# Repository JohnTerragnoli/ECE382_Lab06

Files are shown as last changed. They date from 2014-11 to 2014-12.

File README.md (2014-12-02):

ECE382_Lab06
============

#Purpose

The purpose of this lab is to use pulse width modulation to use an MSP430 to control a small robot car.  This will be done with the help of other devices, such as driver and regulator chips, IR sensors, and a remote.  

#Prelab
**Things to accomplish**

1. Use A regulator to power the MSP430.
2. How to use hardware to achieve robot control (driver).
3. Consider additional hardware you'll need (regulator, motor driver chip, decoupling capacitor).
4. Which pins will output which signals you need.
5. Which side of the motor will you attach these signals to.
6. How will you connect these extra parts?
7. How to use these signals to achieve forward/back/left/right movement.
8. consider how you will setup the PWM subsystem to achieve control.
9. what are the registers you'll need to use.
10. which bits in the registers are important?
11. what's the initialization sequence you'll need?
12. Try to build simple commands, such as moving one motor one direction.
13. Combine simple commands to make complex ones, like just moving in a specific direction.
14. Determine worst-case current draw from your motors (**motor stall current**)

**Remember**

1. Never send voltage to both terminals at once.  

##Hardware Planning Process

**How to Power the MSP430**
1. The MSP430 can only accept 3.3v, whereas the source we have can only output 5v.  We need to use a regulator to drop this voltage.  Should maybe use a small capacitor across the 5V rail to smoth high frequency noise.  This capacitor should be ~0.1uF.  
2. To determine how this should be hooked up, this datasheet was consulted.  It deals with [voltage regulators](http://www.ece382.com/datasheets/LD1117V33.pdf).  This schematic is used below:

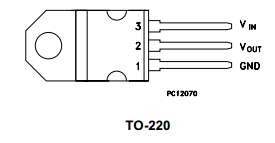
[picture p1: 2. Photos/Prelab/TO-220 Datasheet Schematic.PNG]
TO-220 Config


This was then attached to the MSP430 in the following way:

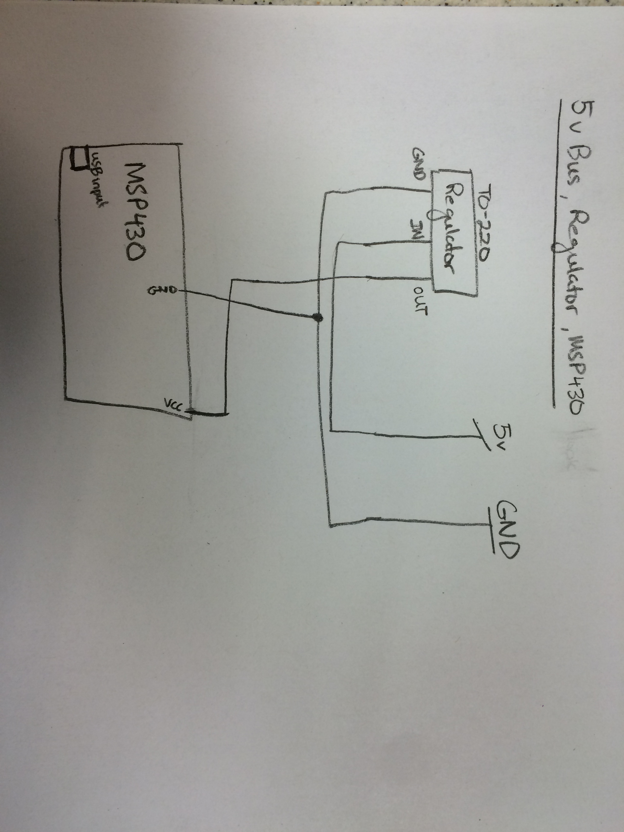
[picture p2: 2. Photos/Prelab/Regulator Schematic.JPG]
MSP Regulator


**Adding the Driver**
The purpose of the driver allows the MSP430 to control the motors without burning up due to the current requirements.  The datasheet for the Quadruple Half Driver can be seen [here](http://www.ece382.com/datasheets/SN754410.pdf).  

Its pinout and function table may be seen below: 

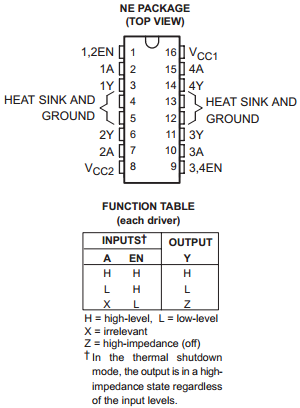
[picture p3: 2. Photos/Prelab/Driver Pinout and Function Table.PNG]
Driver Config


Next, to understand how to hook this up to the motors and to the MSP430, we must first decide how the program will run.  For simplicity sake, I plan on using two individual output signals for the forward direction, and a common output signal for the reverse.  This should make the design easier since we are not required to turn backwards. Therefore, hooking up the driver to the MSP430 and the motos should be relatively easy.  

First, we note that V_cc1 must be between 4.5 and 5.5 volts, as seen in the datasheet.  Therefore, V_ccs1 must be hooked up to the 5v source, which is the only source within range available on the robot.  

Secondly, V_cc2 is meant for the outputs, as noted on the datasheet.  It must be between the range of 4.5 and 36v.  Knowing that the voltage to provide the motors must be greater than 5v, we know that V_cc2 must be hooked up to the 12v source, the only other available source on the chip.  Also, I remember when reading the prelab instructions that if 12v are used, then the duty cycle may not exceed 60%.  This will hurt the motor.  Just something to keep in mind for later.  

Thirdly, the 1,2 EN and 3,4 EN pins will be involved in the logic of the circuit.  Their main purpose is to enable the outputs when their voltage is high.  It would make the most sense for the purposes of this design to make them always high.  Then, the outputs 1-4, or the outputs which are sent to the motors, will be determined entirely by the code.  I think this will lead to fewer complications later on.  Therefore, to do this, the 5v bus will be connected to pins 1, 9, and 16.  

Fourth, the ground must be established for the driver chip.  Based on the pinout, GND is pins 4, 5, 12, and 13.  Therefore, all of these are connected to GND.  

Fifth, I will decide where the inputs (the outputs from the MSP430 go on the driver) will go on the driver chip.  I decide to put one set into pins 3A and 4A, which are pins 10 and 15, respectively.  These inputs will control the right motor through pins 11 and 14, which are ground and input for the right motor, respectively.  Then, the next set of intputs will go into 1A and 2A, which are pins 2 and 7, respectively.  It's outputs are pins 3 and 6, which correspond to input high voltage and the ground input voltage for the Left motor.  Don't worry, this will be shown in a schematic.  

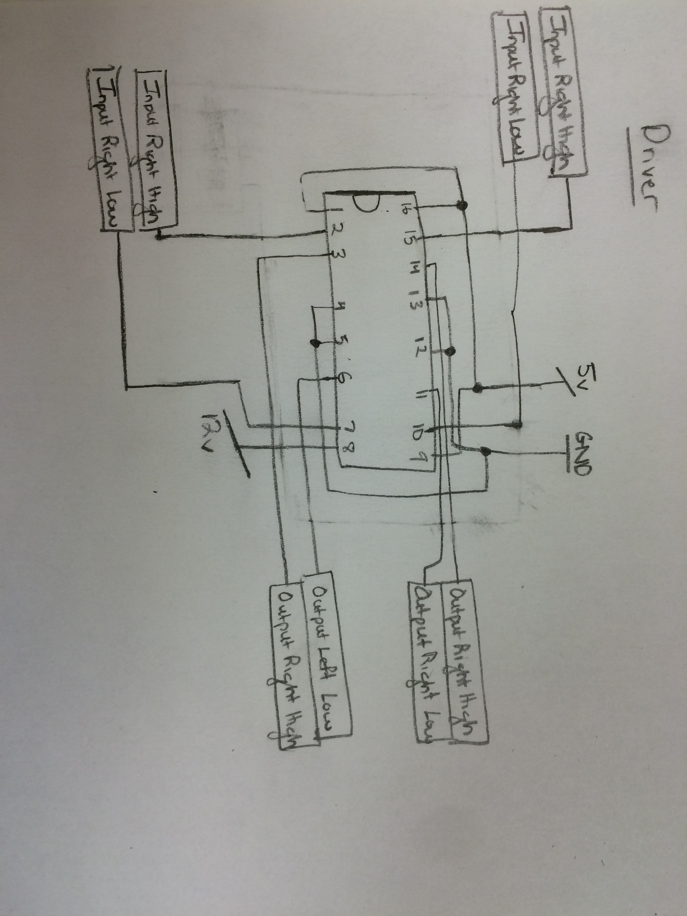
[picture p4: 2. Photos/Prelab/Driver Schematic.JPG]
Driver


**Note:** The four bottom boxes should all be for the "left" motor. I am sorry for writing this down wrong.  

**Choose Outputs for the MSP340**

For simplicity sake, the connections to GND and the regulator made earlier will not be shown again. The outputs will be chosen as below: 

P1.0 = Input Left Low

P1.1 = Input Left High

P2.0 = Input Right High

P2.1 = Input Right Low

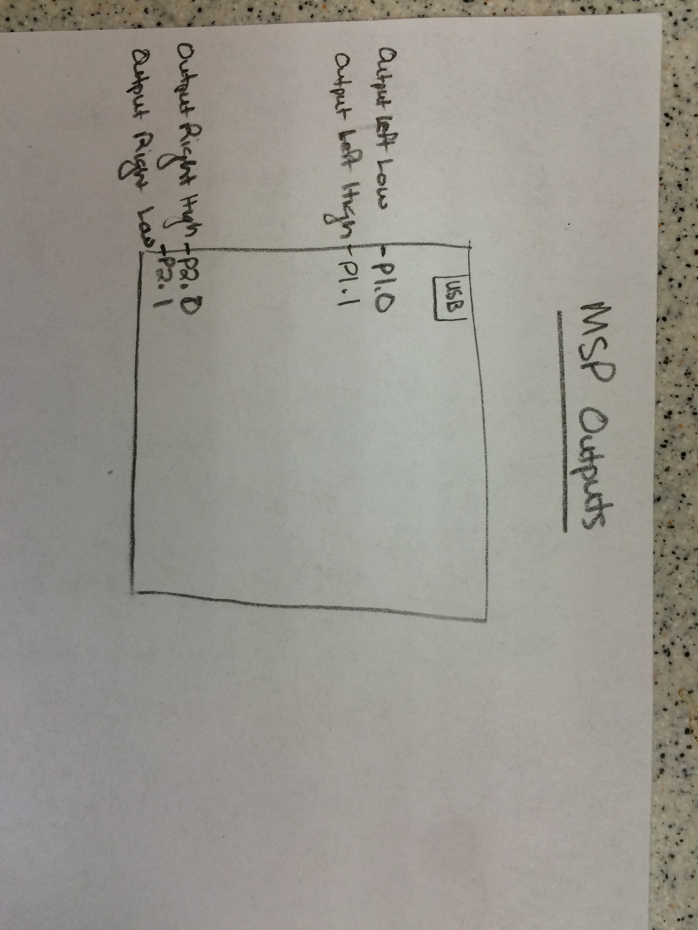
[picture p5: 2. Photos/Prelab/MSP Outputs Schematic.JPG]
MSP Outputs


At this point in the lab I am just assigning the titles "high" and "low" with consistency.  These names might change later if they prove inconvenient.  

**Adding Extra Parts to Circuit**

Only the decoupling capacitor will be added at this moment.  It will be ~100uF, as indicated in the directions, and will be placed across the 5v bus.  Of course the positive end must be placed in the 5v bus!!  No individual schematic is needed for this.  

At this point, all of the hardware for basic functionality was completed.  When A functionality is pursued later, hardware will be developed for that.  

The total schematic can be seen below: 
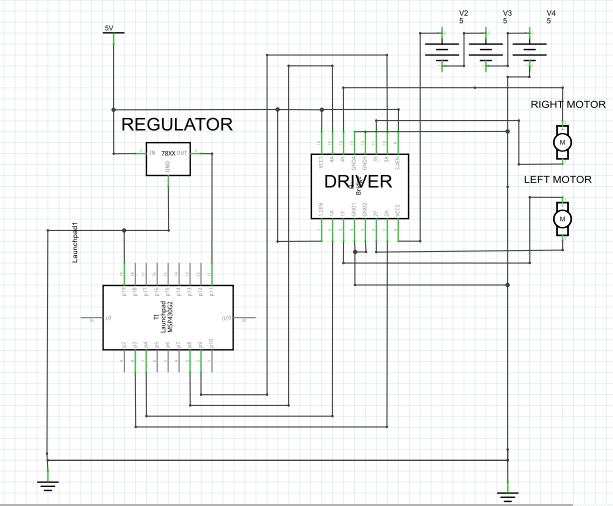
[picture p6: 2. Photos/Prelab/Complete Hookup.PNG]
Total Schematic


This was done using Fritzing software.  To view the file for this software, use [this link](https://github.com/JohnTerragnoli/ECE382_Lab06/blob/master/2.%20Photos/Prelab/Lab06%20Prelab%20Schematic.fzz).  

**IR Sensor**
After I did all of this, I thought it would be smart to add the IR sensor into the circuit early.  To do this, all I needed was ground, power, and the output of the IR (which will be input into the MSP430).

Unfortunately, there was no datasheet for the IR sensor used in class.  However, the pinout is still known.  If looking at the front dot, the right pin is power, the middle pin is ground, and the left pin is the output.  The input voltage will be 3.3v, since this is traveling right to the MSP430.  The ground will be connected witht the rest.  The output of the IR will go to pin P1.7, which was chosen at random.  

The total schematic including the IR sensor can be seen below: 
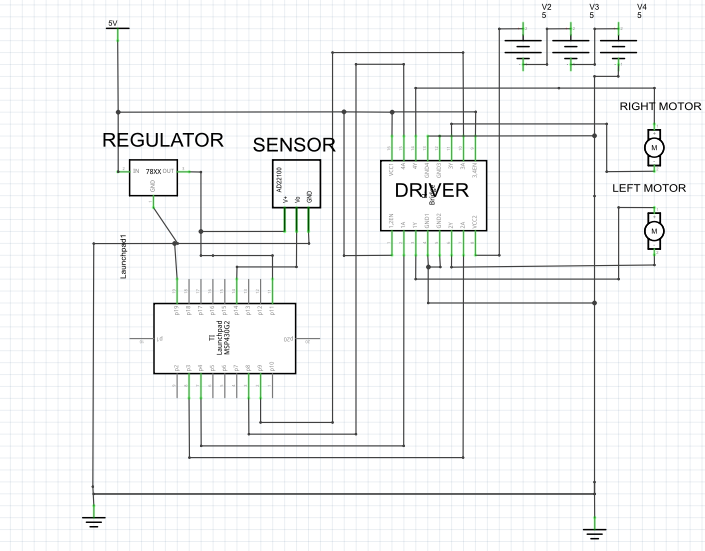
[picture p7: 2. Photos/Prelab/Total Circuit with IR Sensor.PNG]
Everything Hardware


Note: Unfortunately, the correct Fritzing part for the IR sensor could not be found.  Therefore, I just included a part which looked exactly like the sensor, because the only reason for Fritzing is to get the picture anyway.  

This was done using Fritzing software.  To view the file for this software, use [this link](https://github.com/JohnTerragnoli/ECE382_Lab06/blob/master/2.%20Photos/Prelab/Lab06%20Prelab%20Schematic.fzz).  

##Software Planning Process

After this hardware was determined, the software was handled.  This is picking up around number 7 in the list made up top. 

**Achieving Movement**
When a positive voltage is placed across a motor, it will spin forward.  When a negative voltage is applied, it will spin backwards.  To achieve forward movement then, a positive voltage must be applied to both motors.  To make the car turn right, a positive voltage should be applied to the left wheel and the right wheel with no voltage.  To turn left, do the opposite.  The duration of how long a wheel is stopped will determine how sharp the turn is.  To move the car backwards, just apply a negative voltage to the motors.  This can be done easily done by feeding the input to the usually lower terminal of the motor to be above the usually high voltage of the motor.  

**Setting up the PWM**
This will be fairly complicated, since it has never been approached before.  To do this, we will first approximate a PWM of 50%.  It was suggested by Captain Trimble to not exceed 60%, but I would like to play it safe and not blow anything up.  To set this up, I just need to transmit a "high" or the desired voltage difference between my two output pins 50% of the time by constantly turning it on and off.  To do this, I will need two different timers.  This will be useful in case I decide to change the duty cycle later on.  

**Registers to Use**
The TACCTLx, Capture/Compare Control Register will give into on when certain numbers are hit.  
Other handy registers are TACCR0 and TACCR1.  These will be the different numbers we are checking for when counting.  These two numbers will determine the PWM.  When we count to the lower one, turn on the power.  When we count to the higher one, turn off the power.  Start from the beginning and repeat!!  To test this out I will first start with creating a simple program, like a light, and trying to change the brightness using PWM.  

In these registers, the most important bits will be TACTL, the timer which will be stopped and cleared when needed P1/P2DIR and P1/P2SEL, which will help determine the outputs

**Initialization Sequence**
1. Stop the watchdog timer.  
2. Set up the outputs (of the MSP430)
3. Clear the timers
4. decide which clock to use
5. Set the values for TACCR0 and TACCR1
6. Determine the value of the voltage which will be sent to the driver.  
6. Begin the while loop.  

**Simple Commands**
1. spinForward().  This will be done by ensuring that a positive voltage is applied across the motor.  
2. stopSpin().  This will be done by ensuring that no voltage is applied across the motor.
3. spinBackwards().   This will be done by ensuring that a negative voltage is applied across the motor. 

**Medium Commands**
1. moveForward(): ensure both wheels are spinning forward.  Calls the spinForward() command on both wheels.  Ensure that the voltage applied to each wheel is the same.  
2. halt(): makes the car stop moving.  Calls stopSpin() on each motor at the same time. 
3. moveBackwards(): ensure both wheels are spinning backwards.  Calls the spinBackwards() command on both wheels.  Ensure that the voltage applied to each wheel is the same.  
4. fullRight(): calls spinForward() for left motor.  calls stopSpin on right motor for 1 second, then calls spinForward for the right motor as well.  
5. fullLeft(): same concept as fullRight() except switching the wheels used. 
6. halfRight(): same as fullRight except calls stopSpin for 0.5 seconds.  
7. halfLeft():  same as fullLeft except calls stopSpin for 0.5 seconds.  
8. hold(time):  keeps the voltage state of the motors (and the PWM) for a certain amount of seconds).  

**High Commands/Demonstration Commands**
1. basicFunctionality(): moves the car backwards.  halts, moves forwards.  Makes a half right turn, goes straight.  Makes a half left turn, goes straight.  Makes a full right turn, goes straight.  Makes a full left turn, goes straight; moveBackwards(), hold(2), halt(), hold(1), moveForward(), hold(2), halfRight(), hold(1), halfLeft(), hold(1), fullRight(), hold(1), fullLeft(), hold(1), moveStraight(1000).  
2. move will be developed for bragging rights and such later on.  

The flowchart for the code may be seen below: 
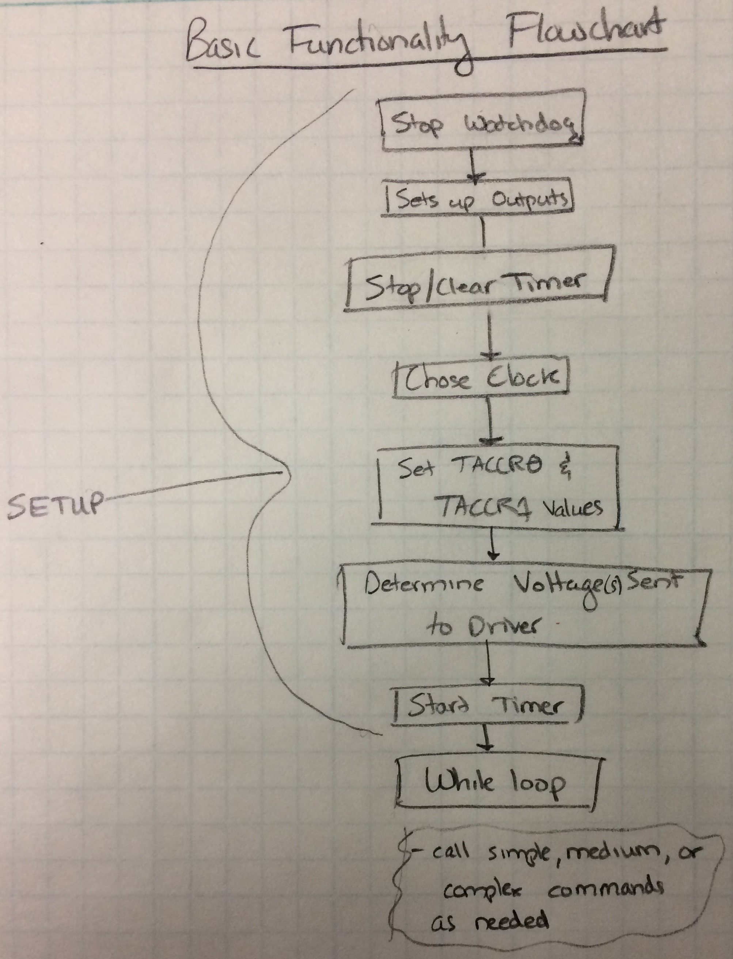
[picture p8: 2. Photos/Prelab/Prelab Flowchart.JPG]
Flowchart


**Worst Case Draw Current**
This has not been found yet.  It will be found in the lab soon, since it is not required for the prelab.  Basically what will be done is to run a specific PWM through the circuit, stopping the wheel forcefully, and measuring the spike in current.  

#Required Functionality

##Creation/Debugging Process

1. For safety purposes, the motor stall current for the motor was then found.  To do this I simply put the voltage source in series with my robot.  I let the wheel run, and then abruptly stopped it.  I noticed that the ampere’s would jumped a little past 1A.  I lowered the voltage until it did not jump above 1A.  The voltage for this to occur was approximately 6.5v.  This means that 6.5/12 = 54%.  The duty cycle can then not go above 54%.  I made my duty cycle 50%, which is within the limits.  
2. The design chosen in the prelab was over complicated.  I did take the time to physically construct my circuit.  When I tried to write my own code though, I got fairly confused and could not get anything to work.
3. To fix this issue, I changed my design to match the schematic Dr. Coulston wrote on the board to help us.  The purpose of his schematic was to give us a starting point.  He also provided code for this starting point.  This starting point can be seen below: 

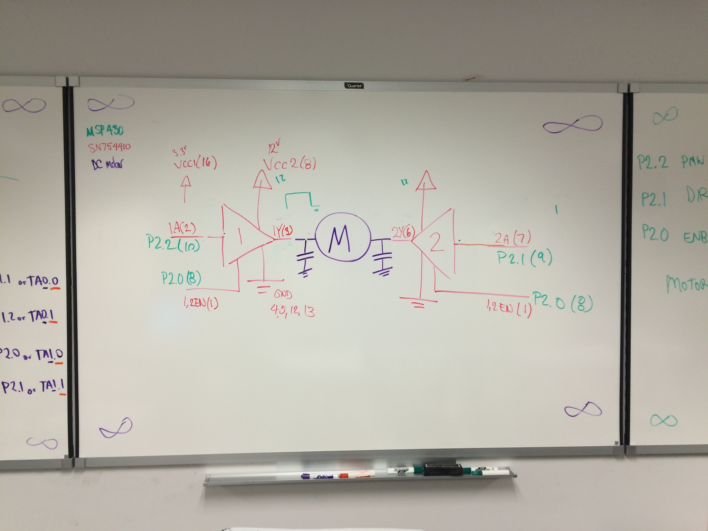
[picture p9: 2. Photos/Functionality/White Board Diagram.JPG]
White Board Drawing


4. The actual and total pinout I used can be seen below: 

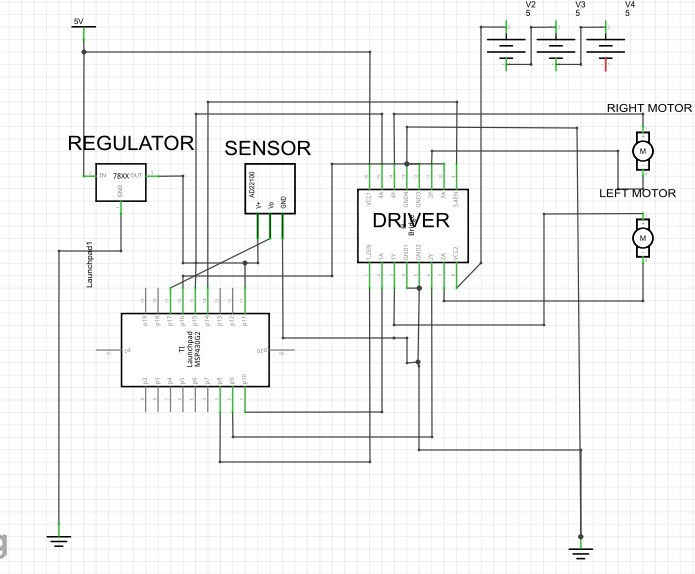
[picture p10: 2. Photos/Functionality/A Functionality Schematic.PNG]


Also, there should be a ground on the negative part of the 12v battery, and each of the batteries should be 4v, not 5v.  

5. The handrawn connections, which were helpful for me to look at, can be seen here: 

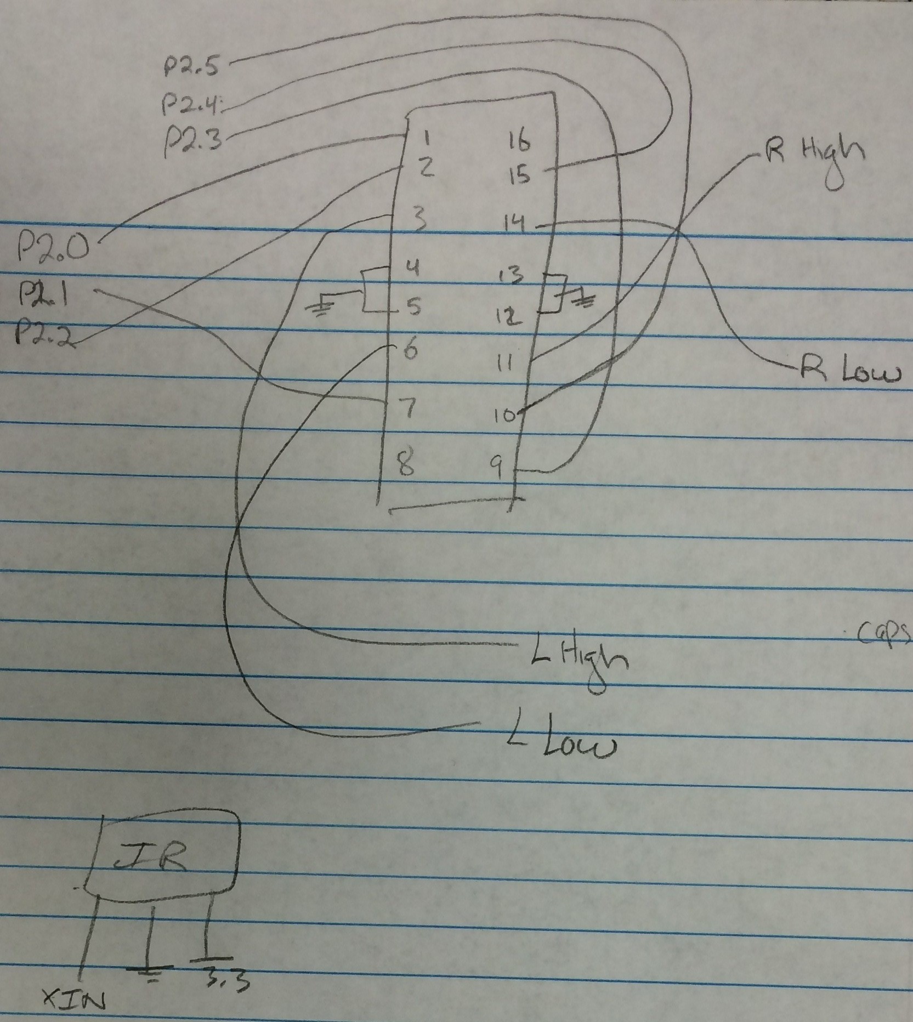
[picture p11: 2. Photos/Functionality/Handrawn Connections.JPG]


6. I then built the schematic on the fly.  Using the code given, I was able to get my car to spin in a circle.  This seemed really exciting to me.  I then commented out different sections of the code to understand what they do.  I realized that P2SEL and P2DIR were both needed to set the wheel direction.  I decided to make functions for these then commands.   I created four functions.  One to either turn forward or backward, or on or off forwards and backwards.  
7. One of the hardest parts was to understand how to get the wheel to move backwards.  What I realized that that the second input to the motor P2.1, was going to be the other input to the motor.  Therefore, if I would P2.1 to a high of 12v, then this would jump over the approximately 6v input to the other side of the motor to make the wheel spin forward.  Because the motor is DC, if a negative voltage is applied across the terminals, then the wheel will spin backwards.  I messes around with what bits to use, but finally settled on BIT1 and BIT5 to make the left and right wheel move back respectively. 
8. A simple problem I had was that once I set the bits 1 and 5 to make the wheel move backwards, I could never change the direction again.  I realized that this was because I never reset the bits 1 and 5 when I wanted to move forward again.  To fix this I simply reset the “backwards” bits when I wanted to travel forward and reset the “forward” bits when I wanted to ravel backwards.  After this occurred, I was able to output what I wanted to the car.  
9. Using the simple commands for starting/stopping and wheel forward/backwards, I was able to create the medium level commands.  These were somewhat unnecessary, if only for simplicity sake.  What they do is just make the wheels work in synchronous, when desired.  
10. Then, I combined these medium commands to functional commands, or moving the car in four directions and two half directions.  This was fairly simple.  A command which was very useful was the delay command, as seen in Dr. Coulston’s code, which was useful in creating turns of different angles.  To do a left turn, the left wheel needs to stop for a certain amount of time while the right one continues to spin.  To do a right turn, the wheels need to do the opposite.  
11. The, I used the delay command to separate the movements of my robot so that it would be easily viewed.  I just combined all of the directional commands into a basic functionality function for simplicity sake.  Captain Trimble actually checked off on this on 11/21/14.  

The text files for required functionality are shown below: 

[Basic Main](https://raw.githubusercontent.com/JohnTerragnoli/ECE382_Lab06/master/1.%20Code/Basic%20Functionality/main.c)
[Basic Header](https://raw.githubusercontent.com/JohnTerragnoli/ECE382_Lab06/master/1.%20Code/Basic%20Functionality/header.h)
[Basic Implementation](https://raw.githubusercontent.com/JohnTerragnoli/ECE382_Lab06/master/1.%20Code/Basic%20Functionality/implementation.c)

#A Functionality

Notice, that the pinout for A Functionality is the same as the one for Required functionality.  The only addition is the sensor coming into the MSP430.  

Full Pinout

Note: The capacitors are not in the schematic, but were used in design.  They were over the 12v and 5v source, all four motor outputs, and the reset button on the MSP430.  The values used were just the ones given in class.  Also, there should be a ground on the negative part of the 12v battery, and each of the batteries should be 4v, not 5v.  

##Creation/Debugging Process

1. First, to do this, I used my code from lab 5 and made sure my remote kept working.  To do this, I temporarily removed the MSP430 from the robot, wired up the IR sensor, and ran my lab05 code for basic functionality.  It still worked, which was a good thing. 
2. I then copied all of my code for the lab 05 basic functionality into my new file for A functionality in lab 06.  This included the header file.  Originally, I used my lab06 basic functionality as the basic shell to achieve A functionality with.  However, this led to multiple issues, and so when I started over I decided to do it the other way.  It worked  
3. The, what I did was wire the IR sensor to the logic analyzer.  I ran the code, pressed a button, and looked at the waveform on the screen.  To my surprise, nothing showed up.  At first I had no idea what was wrong.  Irrationally, I spent a great deal of time checking the code for the MSP430.  What I they did was take a different remote from the class and press a button on it.  The IR sensor and the logic analyzer did in fact pick up the signal from the second remote.  This meant that these two pieces of equipment were working and that my remote probably just wasn’t outputting anything.  Therefore, I went to the lab table and replaced the batteries.  I tried my remote again, and the waveform did show upon the logic analyzer. 
4. I then did a quick check to see if my waveform matched the values I will be using in my header.  They still matched form the last lab.  
5. Once I did this, I tried creating logic statement within the infinite while loop, just to see if the MSP430 was reading the signals correctly.  To try and test this, I tried using a variable, but CCS gave me a really hard time.  I tried using an LED, but this did not work either.  Then, I decided to just go for the gold and include a couple functions, like start not moving and move forward when the up button was pressed.  To my surprise it actually worked and I went over and told Sabin right away.  
6. Once I realized these commands worked, I made four different if statements for the four directions.  I played it
7. When I did this, I realized that on turns the wheel are only stopping half of the time.  This actually did not make sense to me.  While it is not in line with my predictions, it actually make the car turn faster, which is awesome.  Additionally, the button for right or left can just be held down to make it move that direction.  I thought it might have something to do with the reset button, but seeing as that there were no additional problems, I decided not to spend the time “fixing” it.  It was 0100 on a Saturday and I had not started packing for my trip to Japan.  I regret that decision now as I do not have enough sweatshirts and they do not have heat in these buildings.  

The video showing A Functionality can be seen [here](https://www.youtube.com/watch?v=v359o0dWESg&feature=youtu.be).  This was submitted before the due date via email.  

The text files for A functionality are shown below: 

[A Main](https://raw.githubusercontent.com/JohnTerragnoli/ECE382_Lab06/master/1.%20Code/A%20Functionality/A_functionality.c)
[A Header](https://raw.githubusercontent.com/JohnTerragnoli/ECE382_Lab06/master/1.%20Code/A%20Functionality/A_Functionality.h)
[A Implementation](https://raw.githubusercontent.com/JohnTerragnoli/ECE382_Lab06/master/1.%20Code/A%20Functionality/A_Function_Imp.c)

#Analysis/Conclusion/Lessons Learned: 

As a result of this process, I created a working robot which will serve as the backbone for future projects.  The process was difficult, but much was learned.  Motor stall current was finally understood, and how this tells use maximum PWM available to use in design.  Additionally, I learned not to wire up an LED in series by itself because it will get REALLY hot.  I learned ways to get around the fact that we cannot output a negative voltage.  I also learned to place capacitors across voltages so smooth the voltage for certain outputs/inputs.  As a result of doing so, the machine instantly became more reliable. Many other lessons learned are listed in the design process.  

#Grading: 
I got a 100% on all of the functionality and on the prelab.  I have to give you the grading sheet later when I come back from Japan.  

#Documentation:
##Prelab
Only used the datasheets and the picture of the hardware hook up that was give to us by our teachers.  

##Required Functionality
Dr. Coulston’s original schematic.  

##A Functionality
Dr. Coulston’s original schematic.

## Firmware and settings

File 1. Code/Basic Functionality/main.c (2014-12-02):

//-----------------------------------------------------------------
// Name:	JP Terragnoli
// Date:	Fall 2014
// Purp:	Calls the commands for basic funcitonality.
//-----------------------------------------------------------------


#include <msp430.h>
#include "header.h"




void main(void) {

    WDTCTL = WDTPW|WDTHOLD;                 // stop the watchdog timer

    /*P2DIR |= BIT2;							// P2.2 is associated with TA1CCR1
    P2SEL |= BIT2;							// P2.2 is associated with TA1CCTL1

    P2DIR |= BIT4;							// P2.4 is associated with TA1CCR2
    P2SEL |= BIT4;							// P2.4 is associated with TA1CCTL2
*/
    moveForward();

	TA1CTL = ID_3 | TASSEL_2 | MC_1;		// Use 1:8 presclar off MCLK
    TA1CCR0 = 100;						// set signal period

    TA1CCR1 = 50;
    TA1CCTL1 = OUTMOD_7;					// set TACCTL1 to Reset / Set mode

    TA1CCR2 = 50;
    TA1CCTL2 = OUTMOD_3;					// set TACCTL2 to Set / Reset mode


    while (1) {

    	__delay_cycles(STRAIGHTTIME);

    	halt();






    } // end loop

} // end main

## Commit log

2014-11-19 prelab 03
    [Lab06 Prelab Schematic.fzz]
2014-11-19 Prelab 06
    [Lab06 Prelab Schematic.fzz]
2014-11-21 almost finished basic
    [Lab06 Prelab Schematic.fzz]
2014-12-02 finishing readme
    [Lab06 Prelab Schematic.fzz]
